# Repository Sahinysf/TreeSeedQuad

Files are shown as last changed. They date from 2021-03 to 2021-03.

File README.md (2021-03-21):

# SEED SPREADING QUADCOPTER

Have you ever wondered what a world without trees would look like? Close your eyes, and try to imagine a desolate Earth. There'd be no more paper, and everyone would have to resort to technological use - that is, if anyone was left. Trees are a crucial factor to our existence not only because they produce paper, lumber and chewing gum, but because they serve an important role in the carbon cycle.

Ever since the industrial revolution between 1760 and 1840, the world has been in a never-ending carbon chaos. Trees and Plankton are our only saviours in terms of handling this problem, and we can only control one of them, trees.

We need to save trees by protecting them from the destructive human activities like clearance of forests, deforestation for urbanization, etc. Trees are the lungs for the earth. It is an important part of nature’s ecosystem. They balance the soil composition and also act as the barrier for wind and storm. Thus, they provide various uses to the ecosystem. For these reasons, it’s imperative that we save trees.

Since there are a lot of dangerous and difficult-to-reach landsides for humans to plant, the most viable alternative is to use drones for plantation in those regions.

Seed-firing drones will, as the name suggests, fire seeds into fertile soil to allow millions of trees to grow back after being cut down for industrial use. If the rate of planting exceeds the rate of cutting, eventually we will restore the trees we once felled.

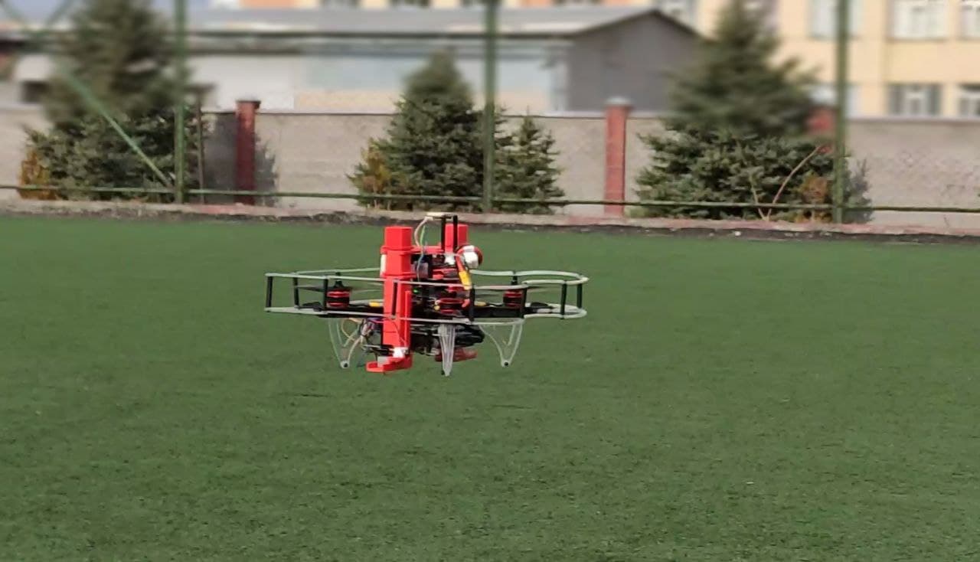
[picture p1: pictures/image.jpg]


## Our Aim

We will make drones able to hold seeds onboard and drop them in an area which we drove in a special application. We can control the density of the seeds and the height of the drop. We also thought about protection of the seeds from insects, animals and dehydration. We choose the earth ball technique invented by Masanobu Fukuoka, aka Fukuoka Technique. This earth ball contains all needed elements to grow, plant seeds and earth for protection. When we drop it on the ground, the earth ball will hold seeds until it gets the needed amount of water and seeds will begin to grow.

Youtube video link - <https://www.youtube.com/embed/Nz1w59v451U>

We achived to do small seeding missions but we faced some problem about autonomous flying with gps.

We coated our battery to protect it from cold weather, seeding missions need to start in winter since apple seeds need to stay in a cold place for some time to break dormacy.

- [Seed capsules](#seed-capsules)

- [How to assemble seeding mechanism to clover 4.2 drone](#how-to-assemble-seeding-mechanism-to-clover-42-drone)

- [How to control the seeding mechanism](#how-to-control-the-seeding-mechanism)

- [Programming](#programming)

## Seed capsules

Fukuoka technique
In southern Japan, the Japanese farmer and philosopher Masanobu Fukuoka invented a seed ball planting technique. The method is regarded as a natural farming technique that requires no machines, no chemicals and very little weeding. By the use of seed balls, land is cultivated without any soil preparation.

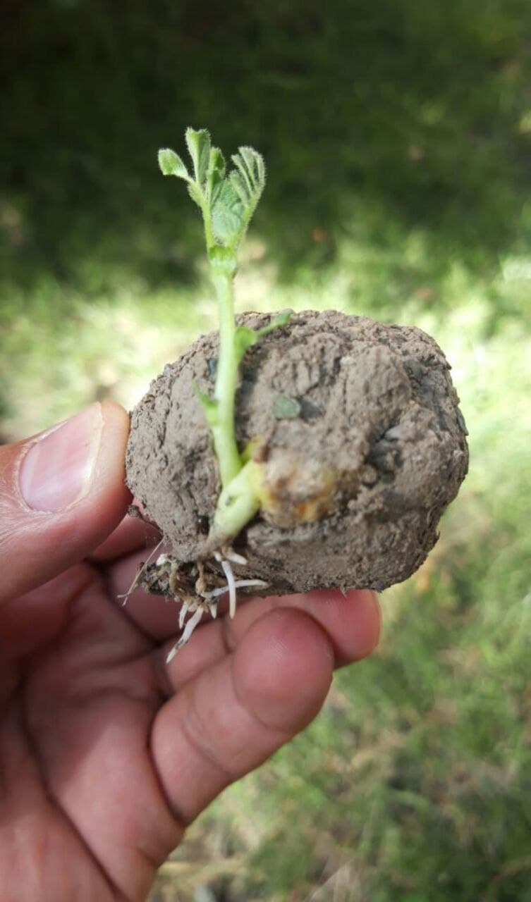
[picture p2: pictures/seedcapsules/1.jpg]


Advantages of seed balls

- It is simple and easier to make seed balls without machines
- Easier for reforestation and plantation in difficult terrains
- Contribute to protect soil, environment and livelihood
- It is an organic technique and doesn’t use any chemicals
- It is a low-cost method compared to traditional afforestation/reforestation techniques
- It requires low maintenance

Which Seeds can be used?

Any seed which grows in your area (In our it’s apple seed)
Size and weight of the seed capsule:
Size and Weight of seed capsules are very important for this project. After some experiments we decided that best size is  16-18mm  diameter and maximum weight is 10 gram

Required materials for making seed balls:

1) 1 bucket Clay
2) 1 bucket Organic Dark Soil / Compost
3) 1 bucket Water (amount of water may vary depending on the soil type)
4) ¼ bucket Seeds

Steps for making seed balls

1) Collect same quantity of both clay and organic soil. For example, if you use one bucket of clay, then you should mix with one bucket of organic soil.
2) Make sure that clay and organic soil fine particles.
3) The clay and organic soil texture should be wet but not sticky
4) Take a bit of mixture and roll it into balls. Test the ball by throwing it on a flat surface. If the ball doesn’t break easily, it means it has got good bonding.
5) Seed balls must be a perfectly round shape otherwise they will be stuck while throwing with the quadcopter
6) Insert seeds (1 to 2 seeds per seed ball for permanent trees such as mahogany, sandalwood, orange, moringa…) (± 5 seeds per seed ball for vegetables, flowers, grasses, clovers…)
7) Dry the seed balls for one to two days in a shaded area, if properly dry, the seed balls will be protected from external predators such as chickens, birds, rats…

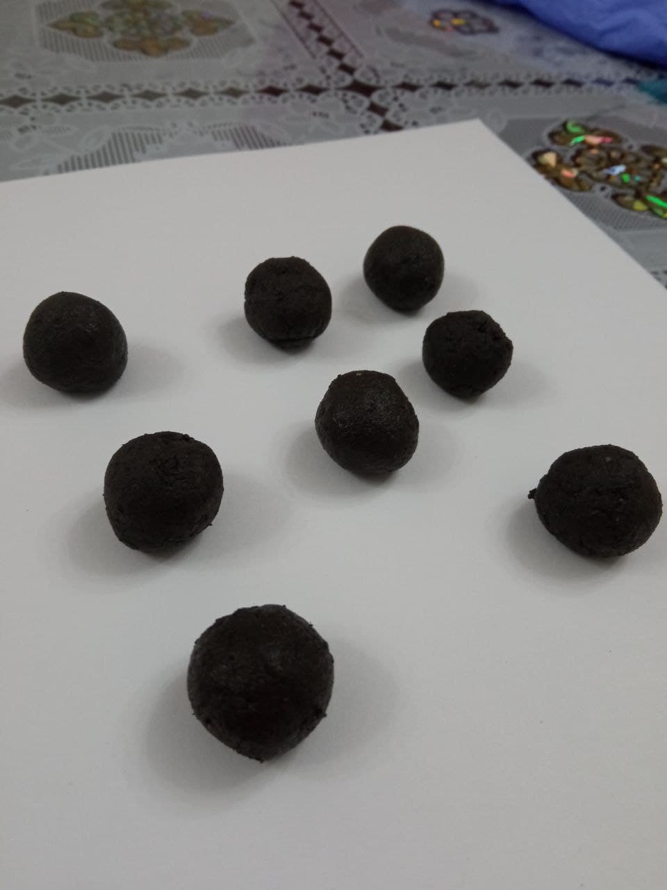
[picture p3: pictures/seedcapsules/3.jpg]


Second technique - Paper seed capsules

This method was influenced by a Korean newspaper that contained seed that could be planted outside after reading it.
                                                                                                                                                              Paper seed capsules :

Required materials :

1) Any kind of Paper
2) Water
3) Blender
4) Seeds

Steps for making paper seed balls:

1) Shredding all of your paper
2) Put paper in blender and add water, after 2 minutes blend.
3) Squeeze all the water out with paper
4) Add seeds and give round shape
5) Let it dry overnight

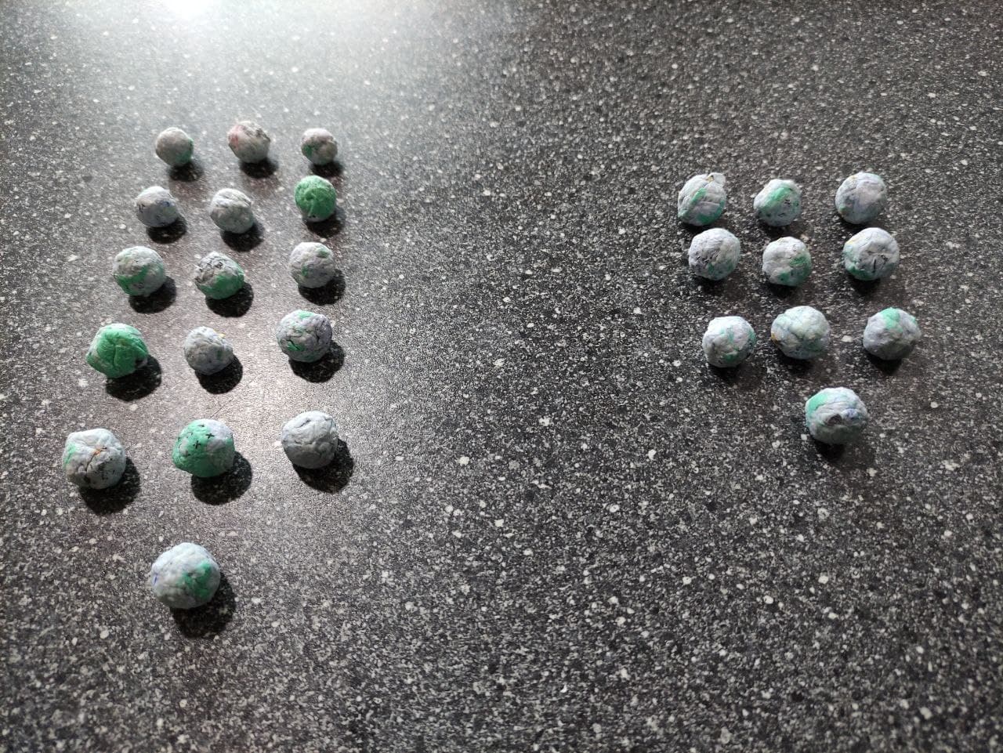
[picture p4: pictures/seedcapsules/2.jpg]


Advantages of paper balls:

- Easy to find materils
- Environmentally friendly

## How to assemble seeding mechanism to clover 4.2 drone

HOW TO ASSEMBLE SEEDING MECHANISM

After finishing step 4, at section Installing guard of Clover 4.2 assembly.

1. Install the Lower Tank Holders to top Deck mount and fix with the M3x8 screws.

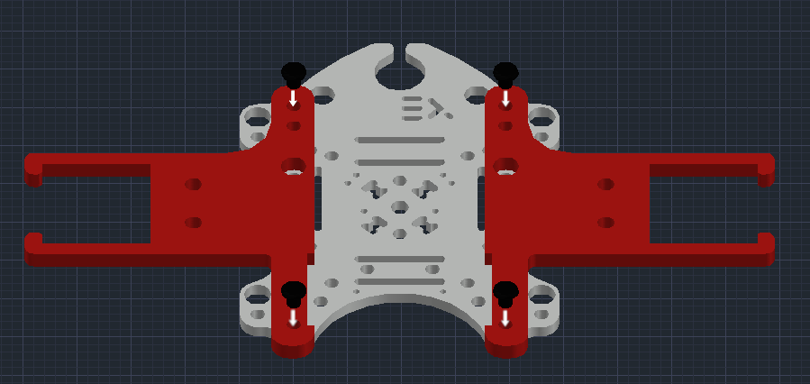
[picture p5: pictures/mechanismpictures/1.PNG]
    

2. Install Nylon rack(40 mm) to 4 sides of the Deck mount.

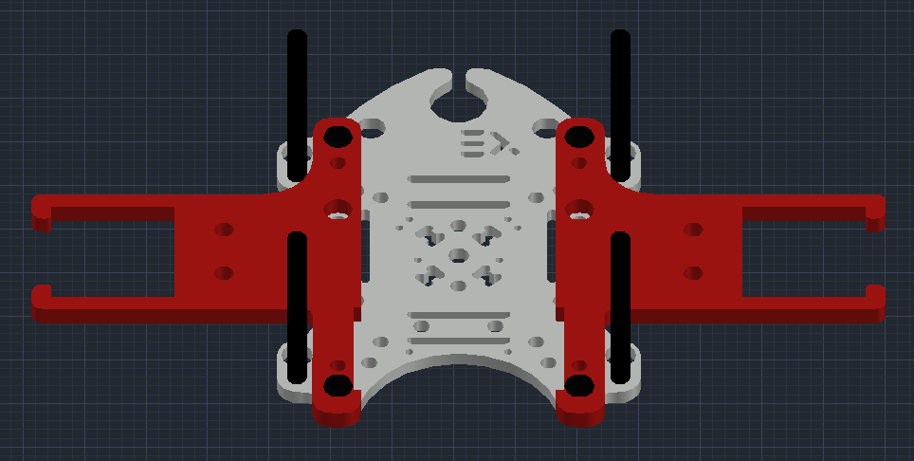
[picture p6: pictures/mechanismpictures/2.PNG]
    

3. Install the Grab deck and fix with the M3x8 screws.

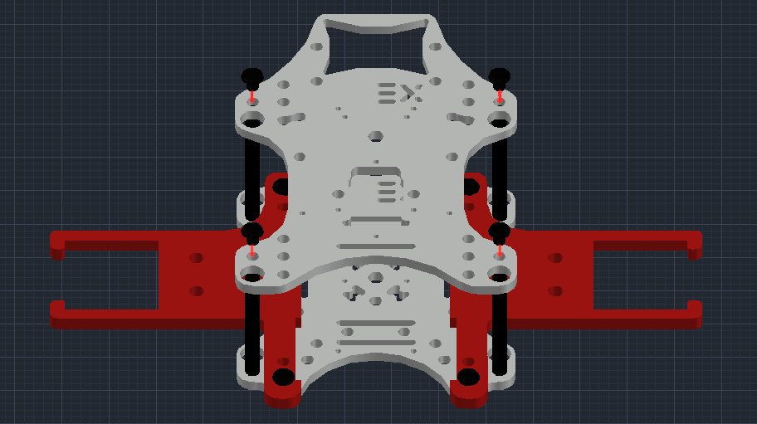
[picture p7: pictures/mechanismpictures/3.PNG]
    

4. Install the Upper Tank Holders to top Grab mount and fix with the M3x8 screws.

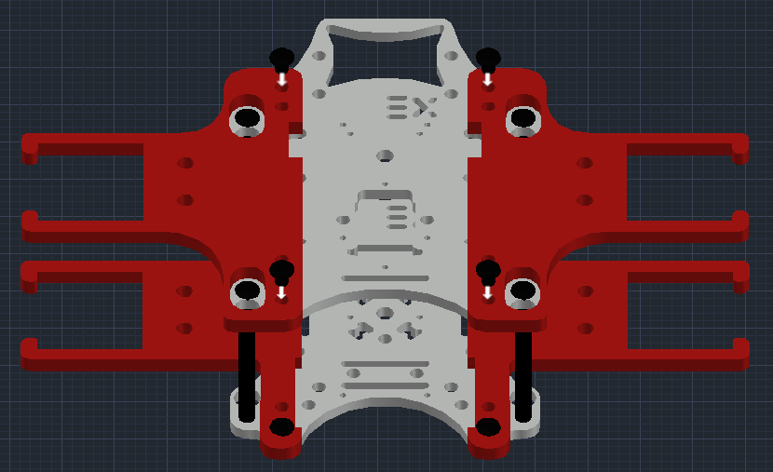
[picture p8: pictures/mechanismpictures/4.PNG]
    

5. Connect the Tanks carefully to Tank Holders.

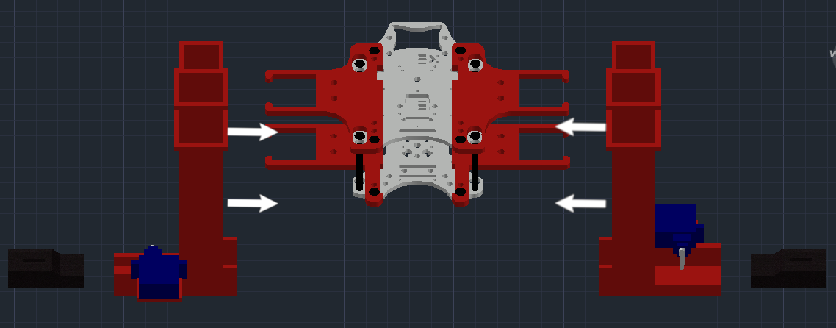
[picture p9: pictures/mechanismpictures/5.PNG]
    

6. Connect SG90 servo motors to Tank using zip tie.

Final view of seeding drone

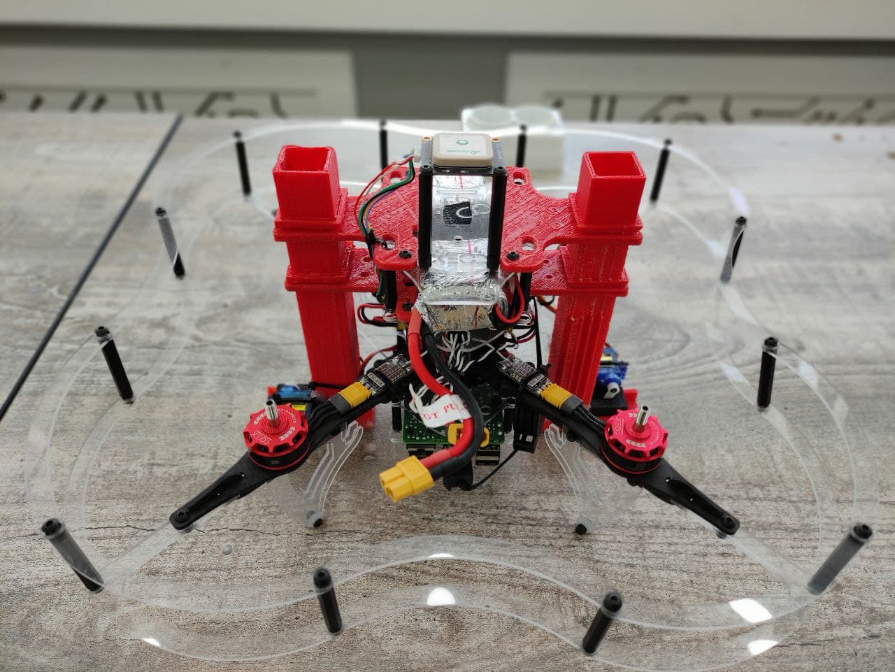
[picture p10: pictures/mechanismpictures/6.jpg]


GPS Module

We installed the GPS Module to the top using 2 Nylon rack(40 mm)

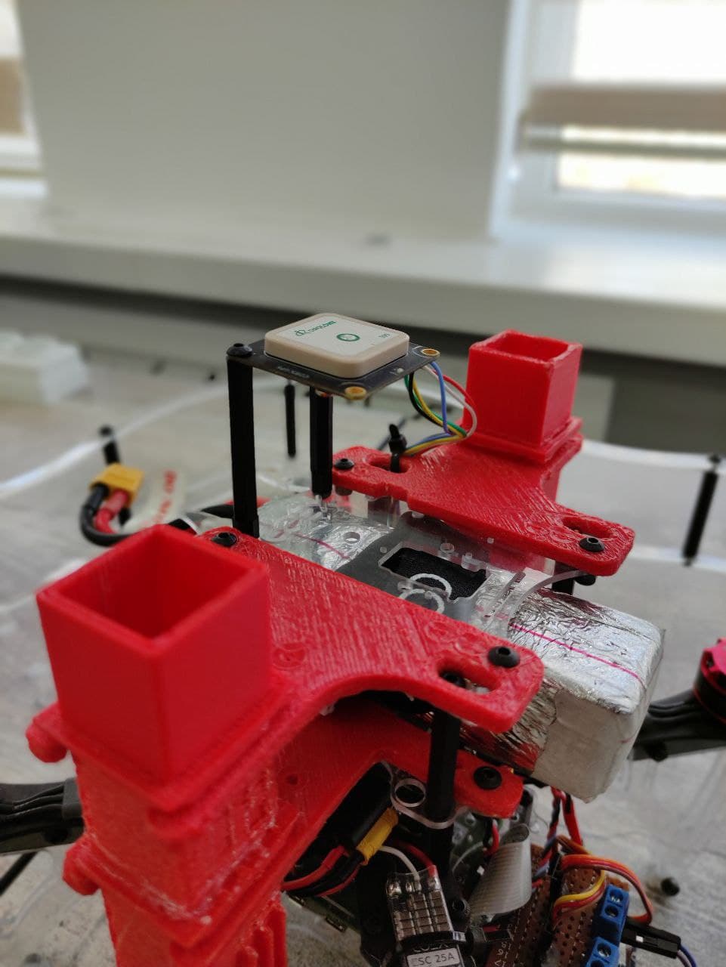
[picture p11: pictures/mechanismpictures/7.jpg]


We coated the battery to protect it from the cold weather

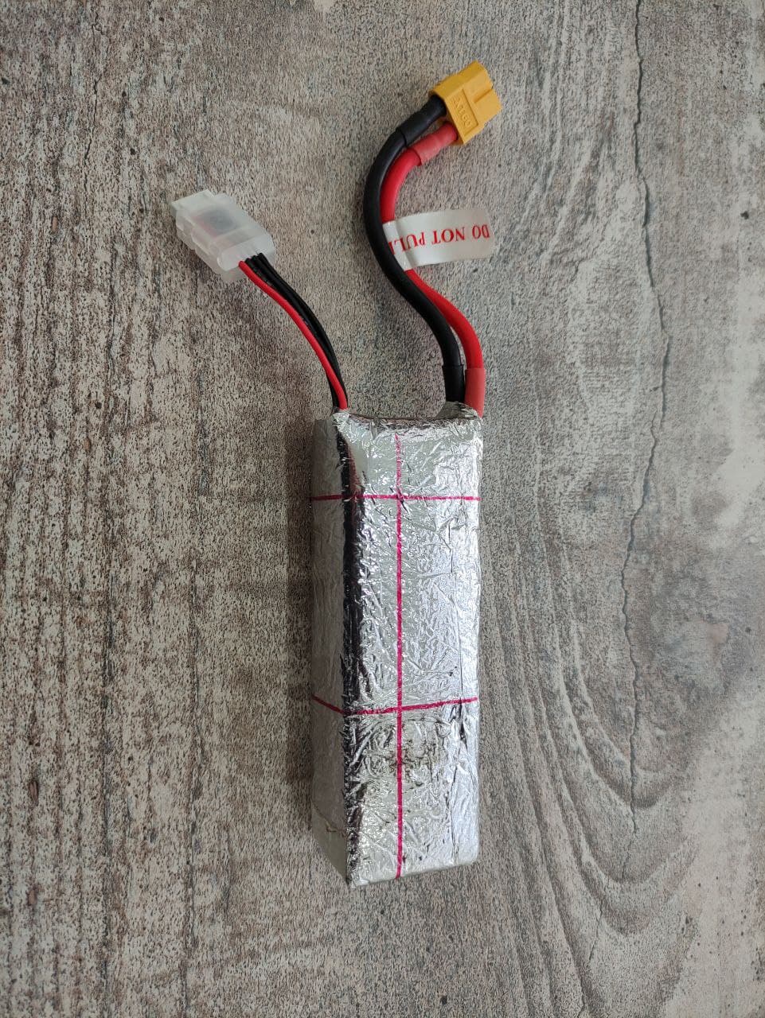
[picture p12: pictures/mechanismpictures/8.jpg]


## How to control the seeding mechanism

Electronic part of seed dropping mechanism consists of:

- Raspberry Pi 4 B of Coex Clover 4
- 2 Micro Servo Motors SG90
- PDB (Power Distribution Board) of Coex Clover 4
Servo motor’s signal pins are connected to Raspberry Pi’s Hardware PWM pins 32 and 33, and power is taken from Power Distribution Board (5 V).

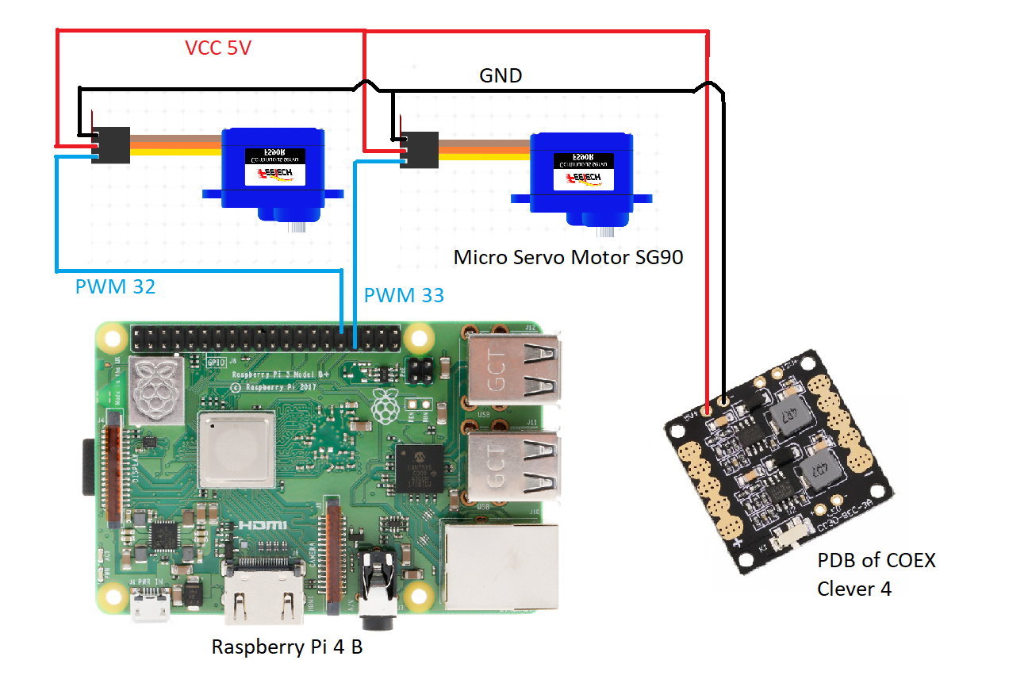
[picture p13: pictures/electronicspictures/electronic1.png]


Explanation of code for controlling servo motors:
Servo motors are controlled using a PWM (Pulse-Width Modulation) signal from Raspberry Pi.
PWM controls the amount of time when signal is HIGH or LOW within a certain period of time.
Duty Cycle – percentage of time when signal is HIGH.
In datasheet below of Servo Motor SG90 duty cycle of each angle of servo motor is represented.
In order to use duty cycle in code we need to convert time to percentage by dividing duty cycle time by the total PWM period.
What we get is:
-90° Rotation Ange or 2ms Duty Cycle => 1/20*100% = 5% Duty Cycle
90° Rotation Angle or 2ms Duty Cycle => 2/20*100% = 10% Duty Cycle
0° Rotation Angle or 1,5ms Duty Cycle => 1,5/20*100% = 7,5% Duty Cycle

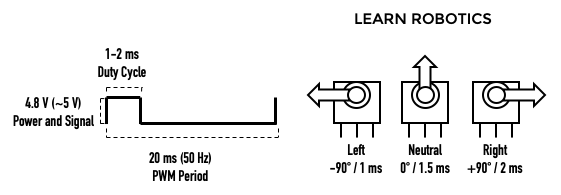
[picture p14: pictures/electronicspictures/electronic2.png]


We’ll do this by using the RPi.GPIO library and writing Python code on the Raspberry Pi.

-First, import the RPi.GPIO library and the sleep function.

```py
import RPi.GPIO as GPIO
from time import sleep
```

-Then, setup the GPIO mode as BOARD

```py
servo = 33
GPIO.setmode(GPIO.BOARD)
GPIO.setup(servo, GPIO.OUT)
```

-Next, create a variable for the servo, pwm. Then, send a 50 Hz PWM signal on that GPIO pin using the GPIO.PWM() function. Start the signal at 0.

```py
pwm=GPIO.PWM(servo, 50)
pwm.start(0)
```

-Use the ChangeDutyCycle() function to write duty cycle percentages to the servo motor.

```py
pwm.ChangeDutyCycle(5) # left -90 deg position
sleep(1)
pwm.ChangeDutyCycle(7.5) # neutral position
sleep(1)
pwm.ChangeDutyCycle(10) # right +90 deg position
sleep(1)
```

## Programming

In order for the mission to be achieavable in the best way and within our reach, we were required to utilize the threading in python.

Simple mission code.

```py
import threading
import time
import rospy
from clover import srv
from std_srvs.srv import Trigger
import RPi.GPIO as GPIO

rospy.init_node('flight')

get_telemetry = rospy.ServiceProxy('get_telemetry', srv.GetTelemetry)
navigate = rospy.ServiceProxy('navigate', srv.Navigate)
navigate_global = rospy.ServiceProxy('navigate_global', srv.NavigateGlobal)
set_position = rospy.ServiceProxy('set_position', srv.SetPosition)
set_velocity = rospy.ServiceProxy('set_velocity', srv.SetVelocity)
set_attitude = rospy.ServiceProxy('set_attitude', srv.SetAttitude)
set_rates = rospy.ServiceProxy('set_rates', srv.SetRates)
land = rospy.ServiceProxy('land', Trigger)

servo1 = 33        # PWM pins
servo2 = 32

GPIO.setmode(GPIO.BOARD)    #set pin numbering system

GPIO.setup(servo1,GPIO.OUT)
GPIO.setup(servo2,GPIO.OUT)

pwm1 = GPIO.PWM(servo1,50)    #create PWM instance with frequency
pwm2 = GPIO.PWM(servo2,50)

pwm1.start(0)        #start PWM of required Duty Cycle 
pwm2.start(0)  

def servo_drop(seconds):   #function to drop seed capsules from 2 tanks
    print("Dropping")

    i = 1                           #variable to choose which tank
    for num in range(seconds/2):
        if(i == 1):                 #first tank
            pwm1.ChangeDutyCycle(10) # release one seed capsule
            time.sleep(0.5)
            pwm1.ChangeDutyCycle(5) # push then drop the capsule
            time.sleep(0.5)
            i = 2                   #changing the variable for to use the second tank in next dropping       
            
        elif(i == 2):               #second tank
            pwm2.ChangeDutyCycle(10) # release one seed capsule
            time.sleep(0.5)
            pwm2.ChangeDutyCycle(5) # push then drop the capsule
            time.sleep(0.5)
            i = 1                   #changing the variable for to use the first tank in next dropping 

        print(num)
        time.sleep(2)

if name == "main":
    # Take off and drone 10m above the ground
    navigate(x=0, y=0, z=10, frame_id='body', auto_arm=True)

    # rospy waits for 10 seconds to take off
    rospy.sleep(10)

    # Dropping starts simultaneuously with flying forwards 5 meters
    d = threading.Thread(target=servo_drop, args=(18,))  # 18 is the sum of all the time that the drone hovers after take off
    d.start()

    navigate(x=5, y=0, z=0, frame_id='body')

    #rospy waits for 8 seconds to fly foward
    rospy.sleep(8)

    # Fly right 1 m
    navigate(x=0, y=1, z=0, frame_id='body')

    #rospy waits for 2 seconds to fly right
    rospy.sleep(2)

    # Fly backward 5 m
    navigate(x=-5, y=0, z=0, frame_id='body')

    #rospy waits for 8 seconds to fly backward
    rospy.sleep(8)

    # Perform landing
    land()

pwm1.stop()
pwm2.stop()
GPIO.cleanup()
```

## Developed by Team MINIONS

### Special thanks to International Ala-Too University for funding Clover 4 kits



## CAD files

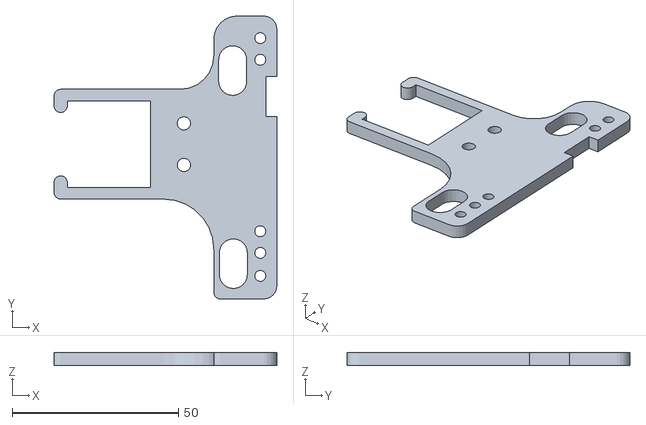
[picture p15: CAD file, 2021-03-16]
CAD/UPPER_TANK_HOLDER_LEFT.stl
66.9 x 85.0 x 4.00

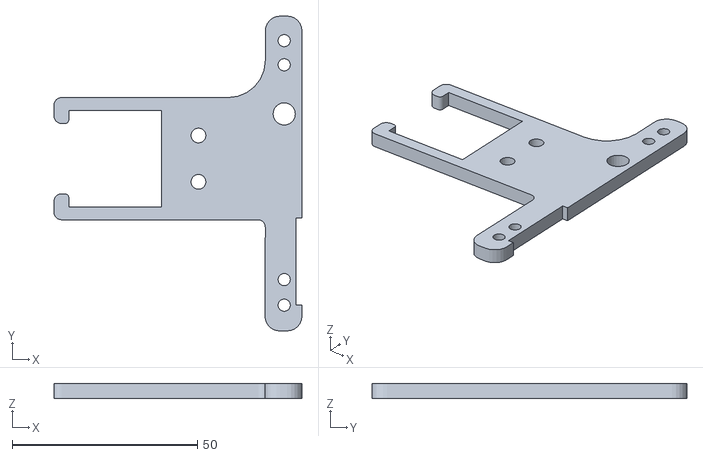
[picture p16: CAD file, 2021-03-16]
CAD/LOWER_TANK_HOLDER_LEFT.stl
67.0 x 85.0 x 4.00

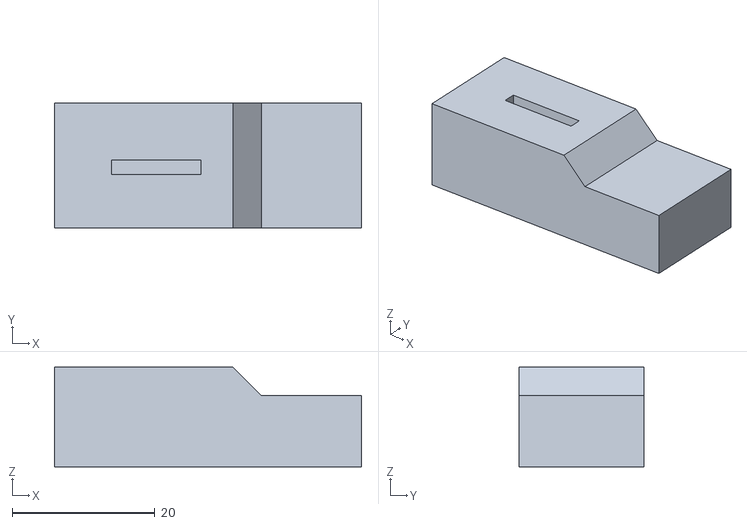
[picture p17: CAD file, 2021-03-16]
CAD/PUSHER.stl
43.0 x 17.5 x 14.0

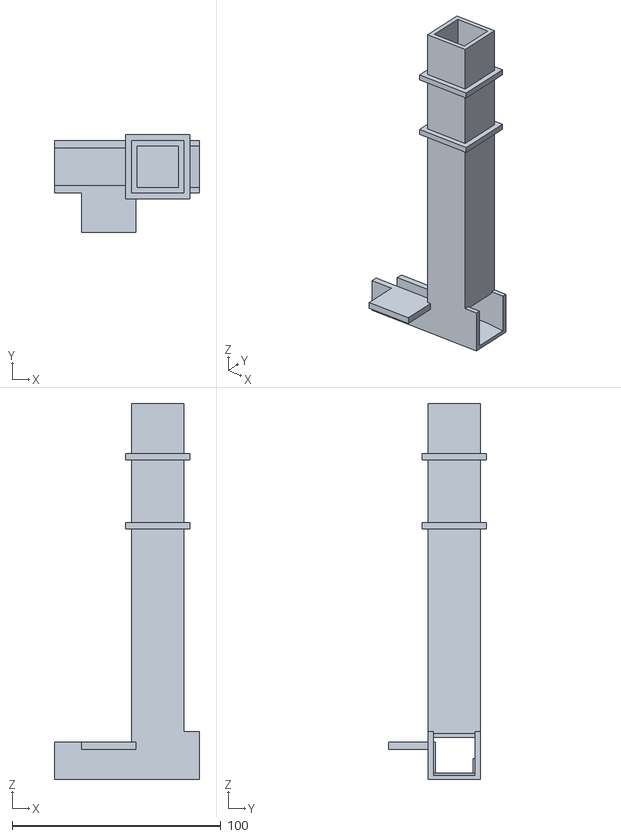
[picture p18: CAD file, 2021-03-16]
CAD/TANK.stl
69.5 x 47.0 x 180.0

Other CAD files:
CAD/UPPER_TANK_HOLDER_RIGHT.stl
CAD/LOWER_TANK_HOLDER_RIGHT.stl
CAD/ALL.dwg

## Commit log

2021-01-27 Create Cad Files
2021-02-27 Update and rename SeedDroppingMechanism/codes/seed_motor.py to SeedDroppingMechanism/servoSeedDropperFlight.py
